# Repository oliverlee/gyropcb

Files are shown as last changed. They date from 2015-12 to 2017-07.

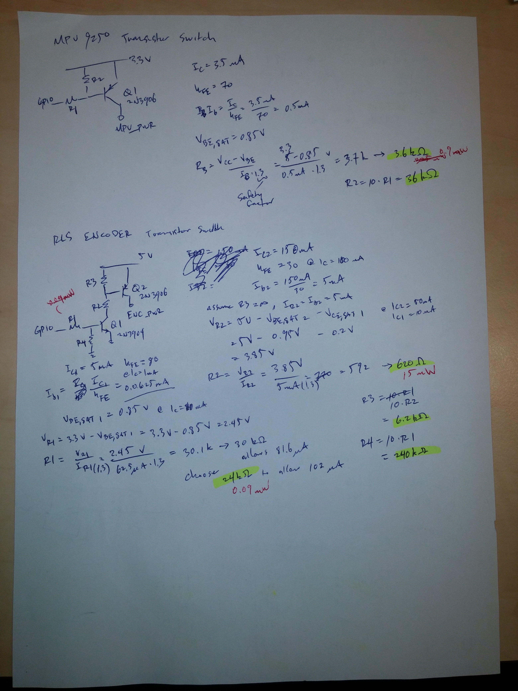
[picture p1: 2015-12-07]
design/IMG_20151120_180757.jpg

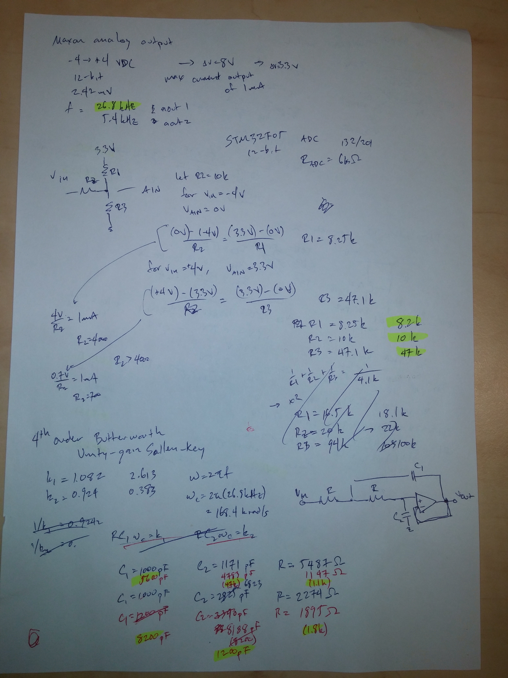
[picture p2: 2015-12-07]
design/IMG_20151120_180812.jpg

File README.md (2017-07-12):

This set of PCBs are designed to use with various projects in the
[phobos](https://github.com/oliverlee/phobos) repository. The PCBs are designed
to be used with the following items:
- [OLIMEX STM32-H405](https://www.olimex.com/Products/ARM/ST/STM32-H405/)
- [Maxon ESCON Module 50//5](http://www.maxonmotor.com/maxon/view/product/control/4-Q-Servokontroller/438725)

## Bill of Materials
The bill of materials is maintained [here](https://docs.google.com/spreadsheets/d/1CJe4dBAEXy64Y3e8YSP1X_Nll6x3aowWz7-QJbUk4VQ/edit?usp=sharing)

It may be out of date so take a look at it carefully.

## Notes
- In order to use the SDIO peripheral, R27 on the OLIMEX STM32-H405 must be
  disconnected from from the SDIO_CMD line (EXT1-11). This can be done by
  cutting the trace connecting EXT1-11 and R27.

## Errata
### v0.1
### mc pcb
- Description for solder jumper switch S3 on silkscreen layer is reversed.
- Description for solder jumper switch S4 on silkscreen layer is reversed.
- SDIO CMD line missing pullup resistor. A 33k resistor can be added at EXT1
  connecting pins 5 and 11. The leads must be kept as short as possible to
  minimize overshoot and ringing.

### power pcb
- +24V mount pad not connected to +24V rail.
- GND mount pad not connected to ground planes.
- The measure line of the Kistler torque sensor cannot be pulled to ground. A
  fix requires the removal of transistor Q2 and the measure line to be connected
  to the collector end of transistor Q1. This bypasses and disables switch S1.
- Description for solder jumper switch S2 on silkscreen layer is reversed.
- Silkscreen on J1, J3 incorrect: WIND1 and WIND2 reversed.
- Trace for HALL2_S2 between Ext3 and J3 is completely missing.
- J1, J3 molex pins can not withstand motor windings 1,2,3 current. Motor windings cable must be connected directly to motor dive. Check drawing for new molex types used to rearrange the new connection.
- J1, J2 male molex vertical headers must be changed with right hand angle headers to allow motor drive fit to Ext2 & Ext1. Check drawing file for new headers used to make the rearrangement.

For the steer by wire bicycle project the following changes were made:
### power pcb
18 Voltage regulator switched from LM2576S TO LM2576HV to withstand higher voltage since power supply voltage was switched from 24v to 36v.
### mc_pcb
Multiplexers 74AC157D were removed since Giel mentioned that there was an issue with the supply voltage. 
The inputs and outputs pins of the multiplexers were connected with cables. U4 now gives an output of ENC1_CHA+CHB and ENC2_CHA+CHB. 
Rear wheel encoder must be connected directly to microcontroller. U5 gives the output of PEDAL_ENC_A +ENC_B.

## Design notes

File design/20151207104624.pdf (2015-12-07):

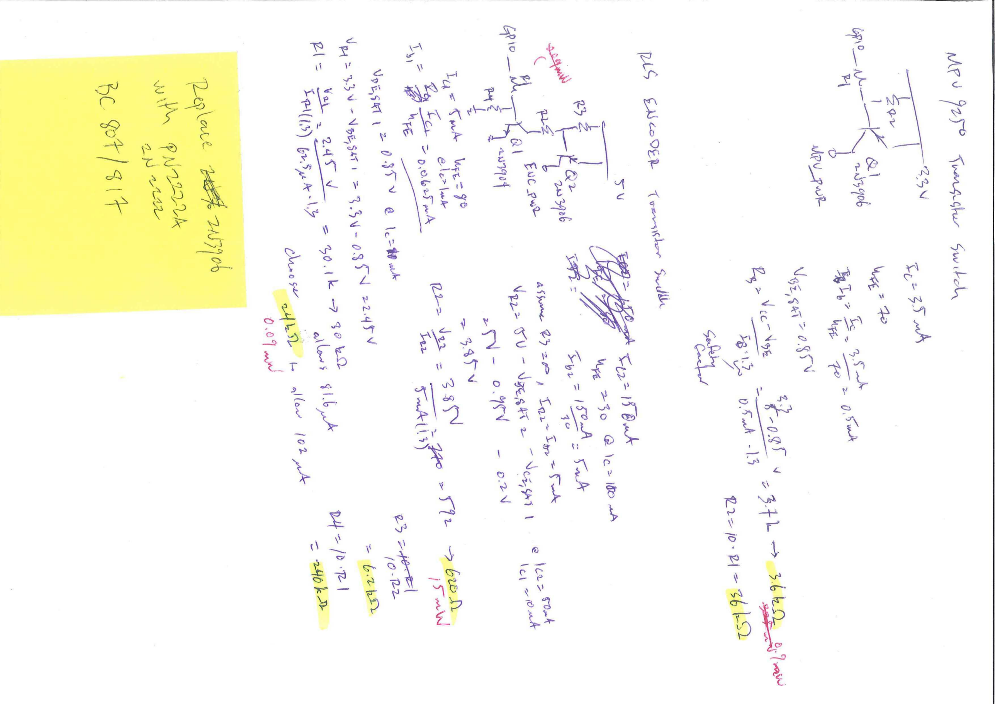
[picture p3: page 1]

- A

V
V

c

r
t

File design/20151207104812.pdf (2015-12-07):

5^

I

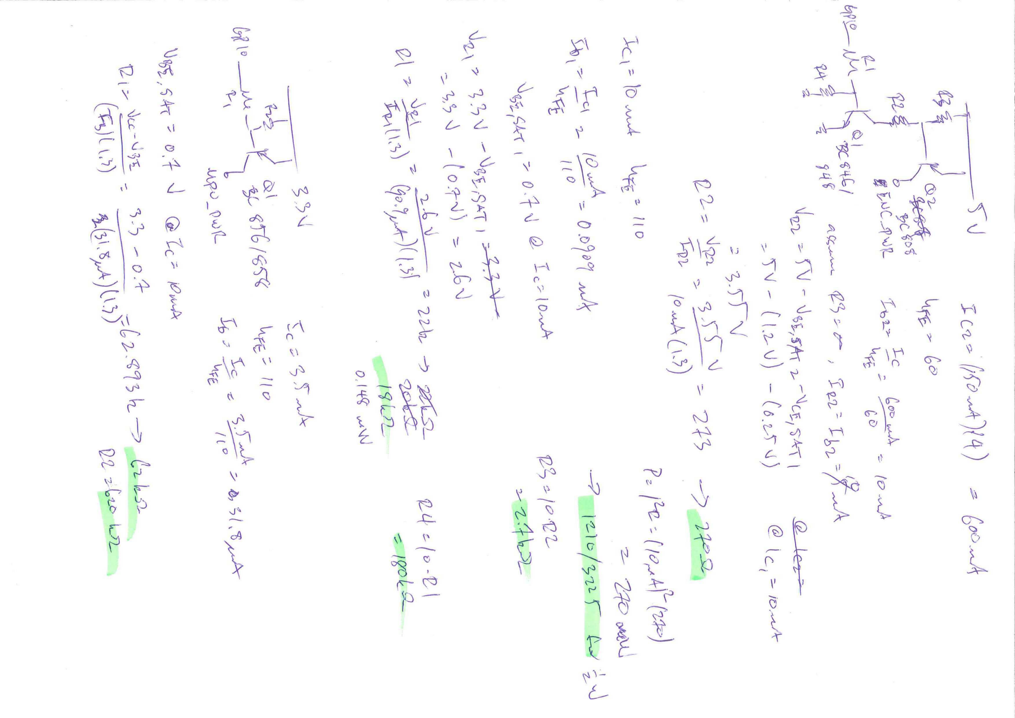
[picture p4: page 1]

I c -

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
0 | ^

4

'3
2

V
1 1 ^

1

&

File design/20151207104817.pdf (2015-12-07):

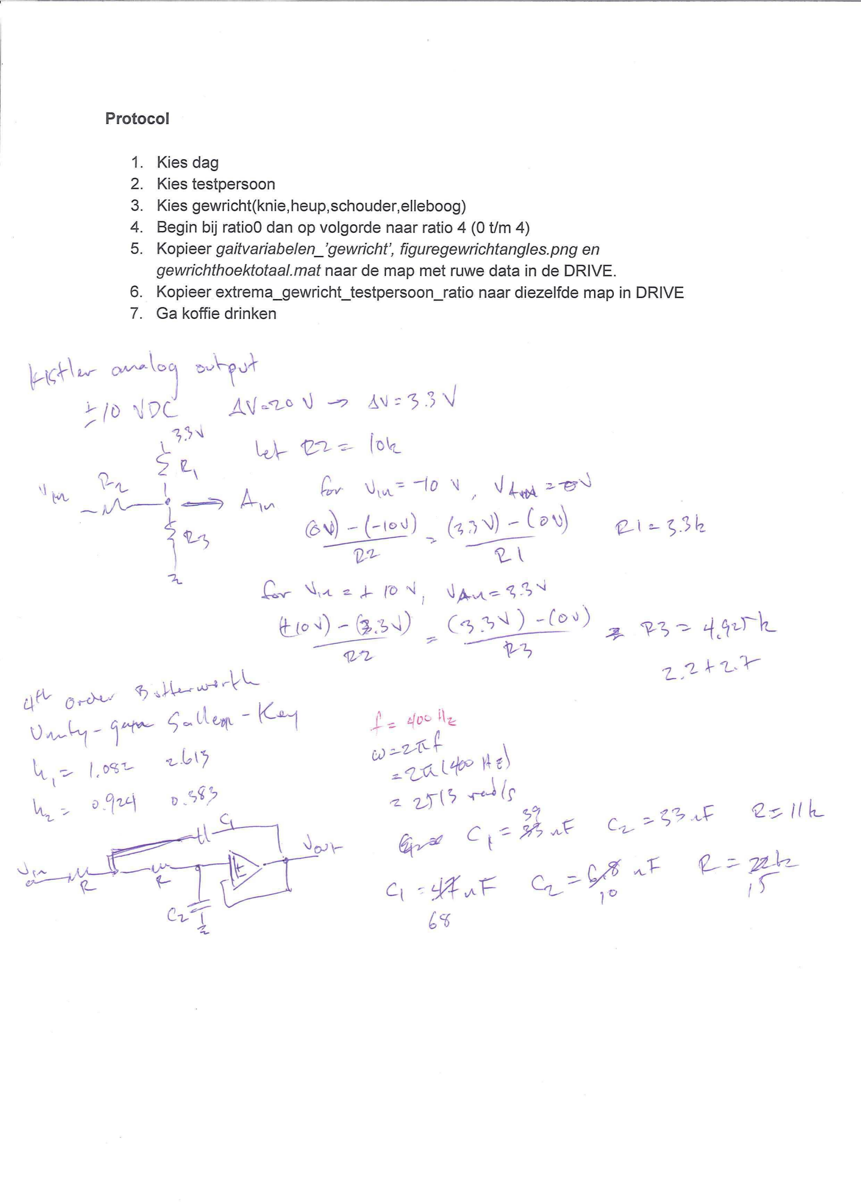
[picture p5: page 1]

Protocol

1. Kies dag
2. Kies testpersoon
3. Kies gewriclit(knie,heup,schouder,elleboog)
4. Begin bij ratioO dan op volgorde naar ratio 4 (O t/m 4)
5. Kopieer gaitvariabelen_'gewricht', | figuregewrichtangles.png | en
gewrichthoel<totaal.mat naar de map met ruwe data in de DRIVE.
6. Kopieer extrema_gewricht_testpersoon_ratio naar diezelfde map in DRIVE
7. Ga koffie drinken

O

### Cv- "O

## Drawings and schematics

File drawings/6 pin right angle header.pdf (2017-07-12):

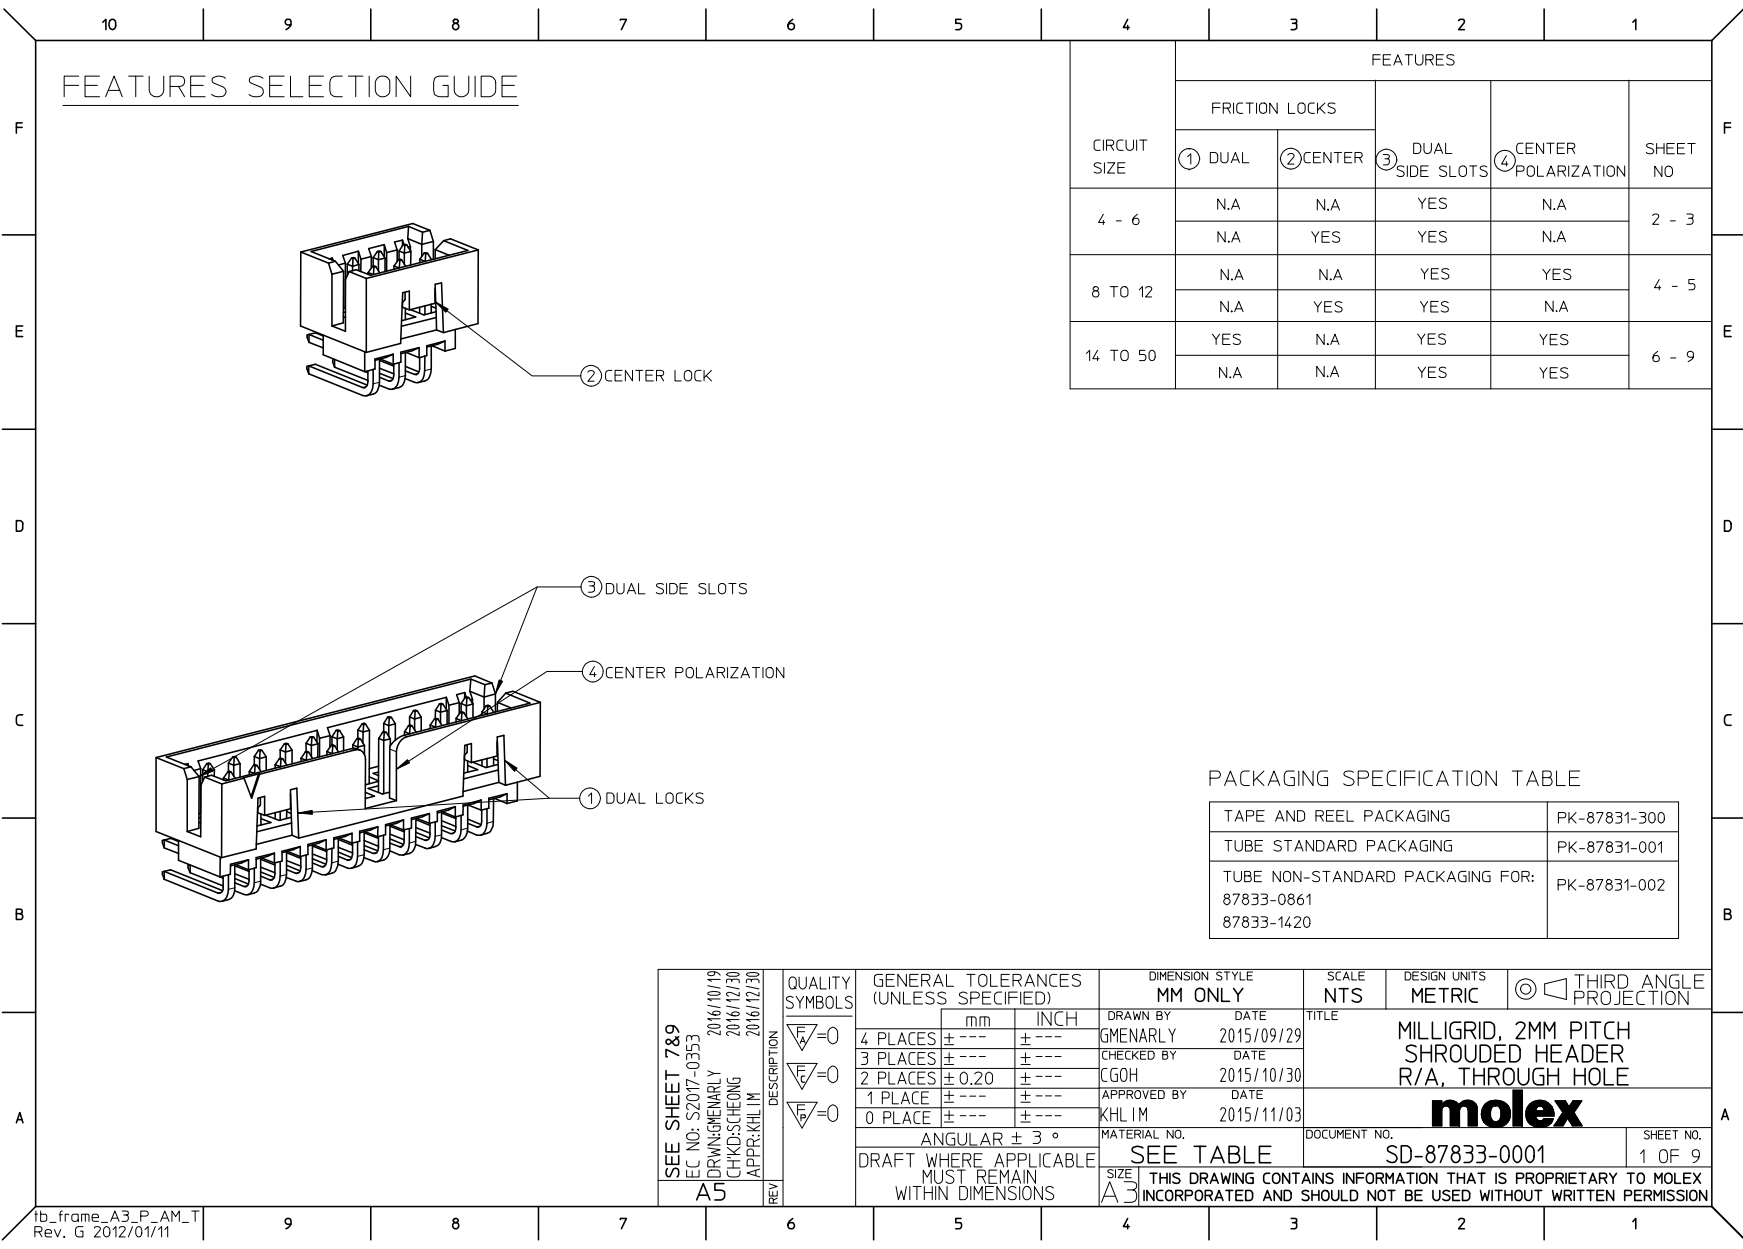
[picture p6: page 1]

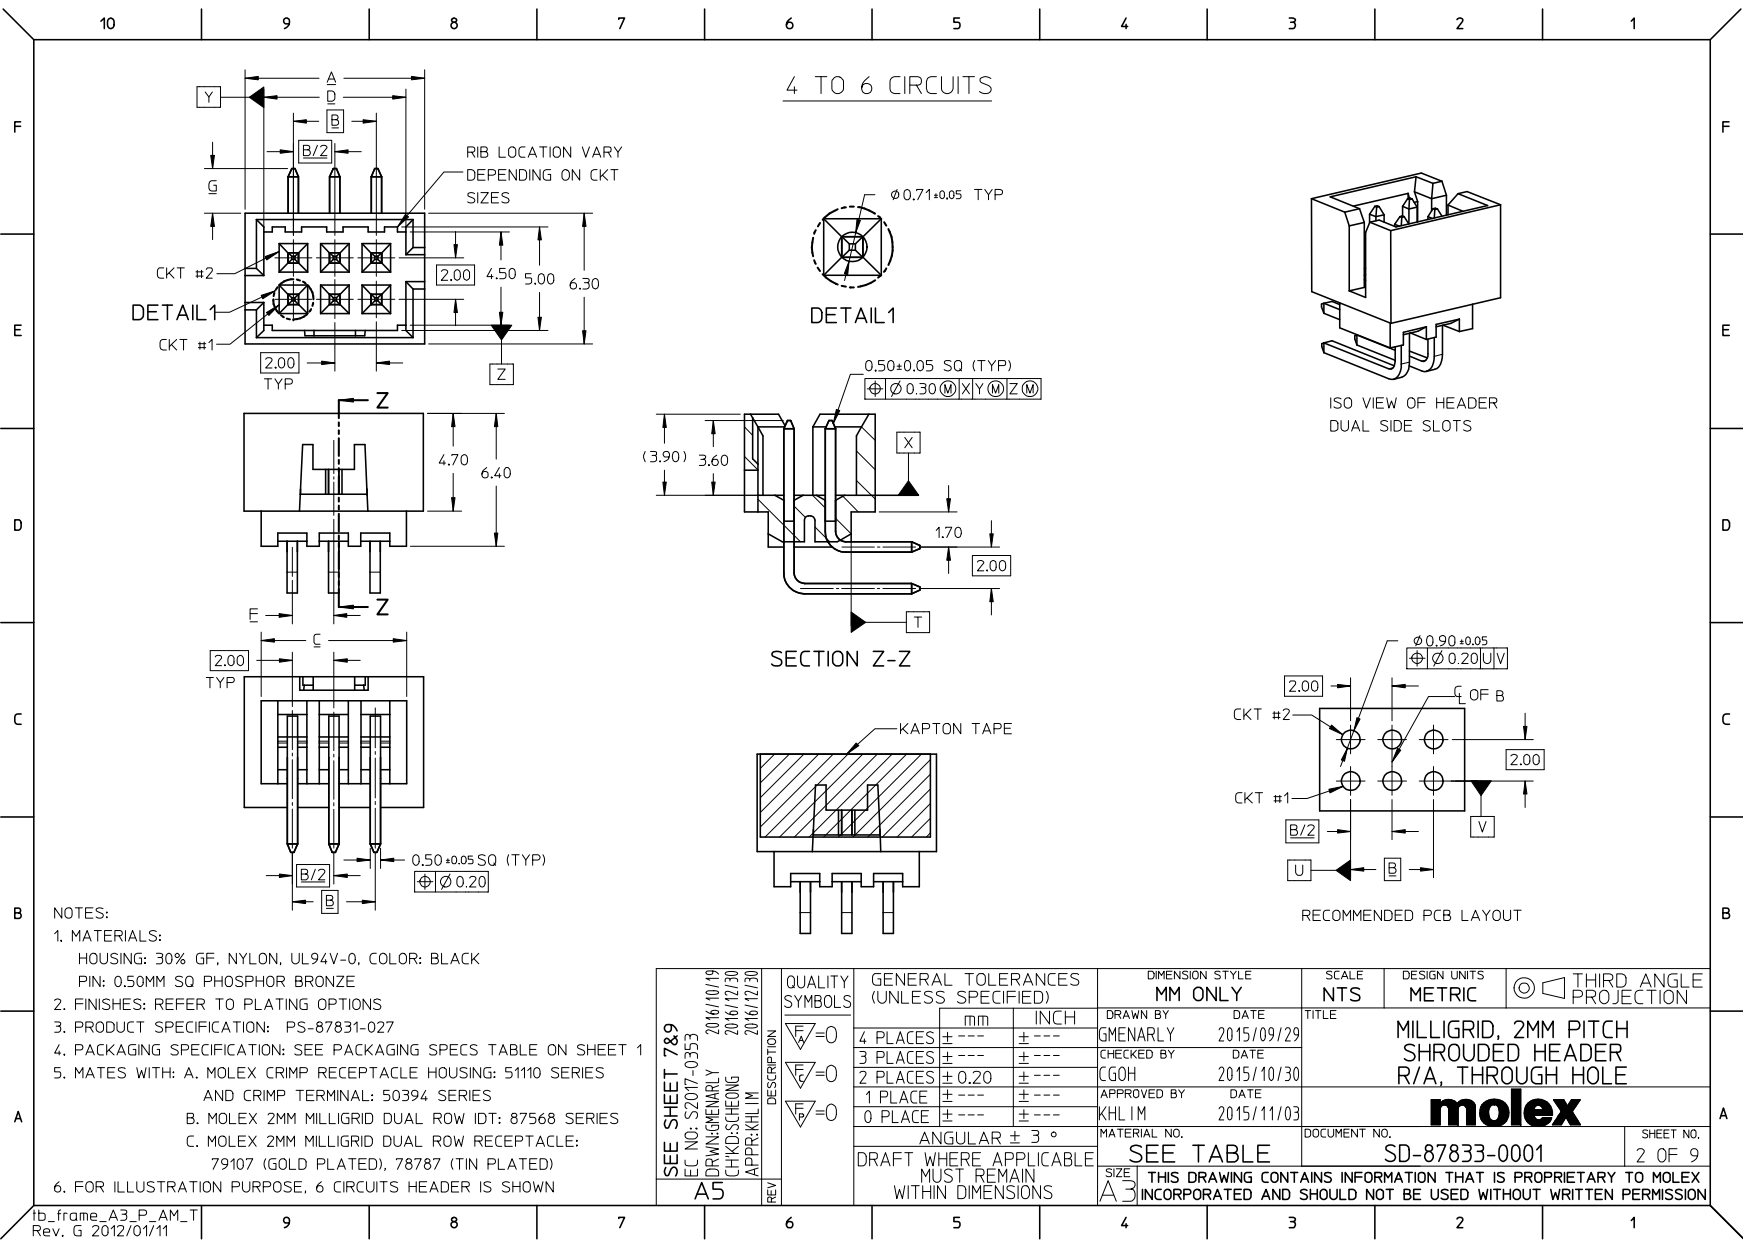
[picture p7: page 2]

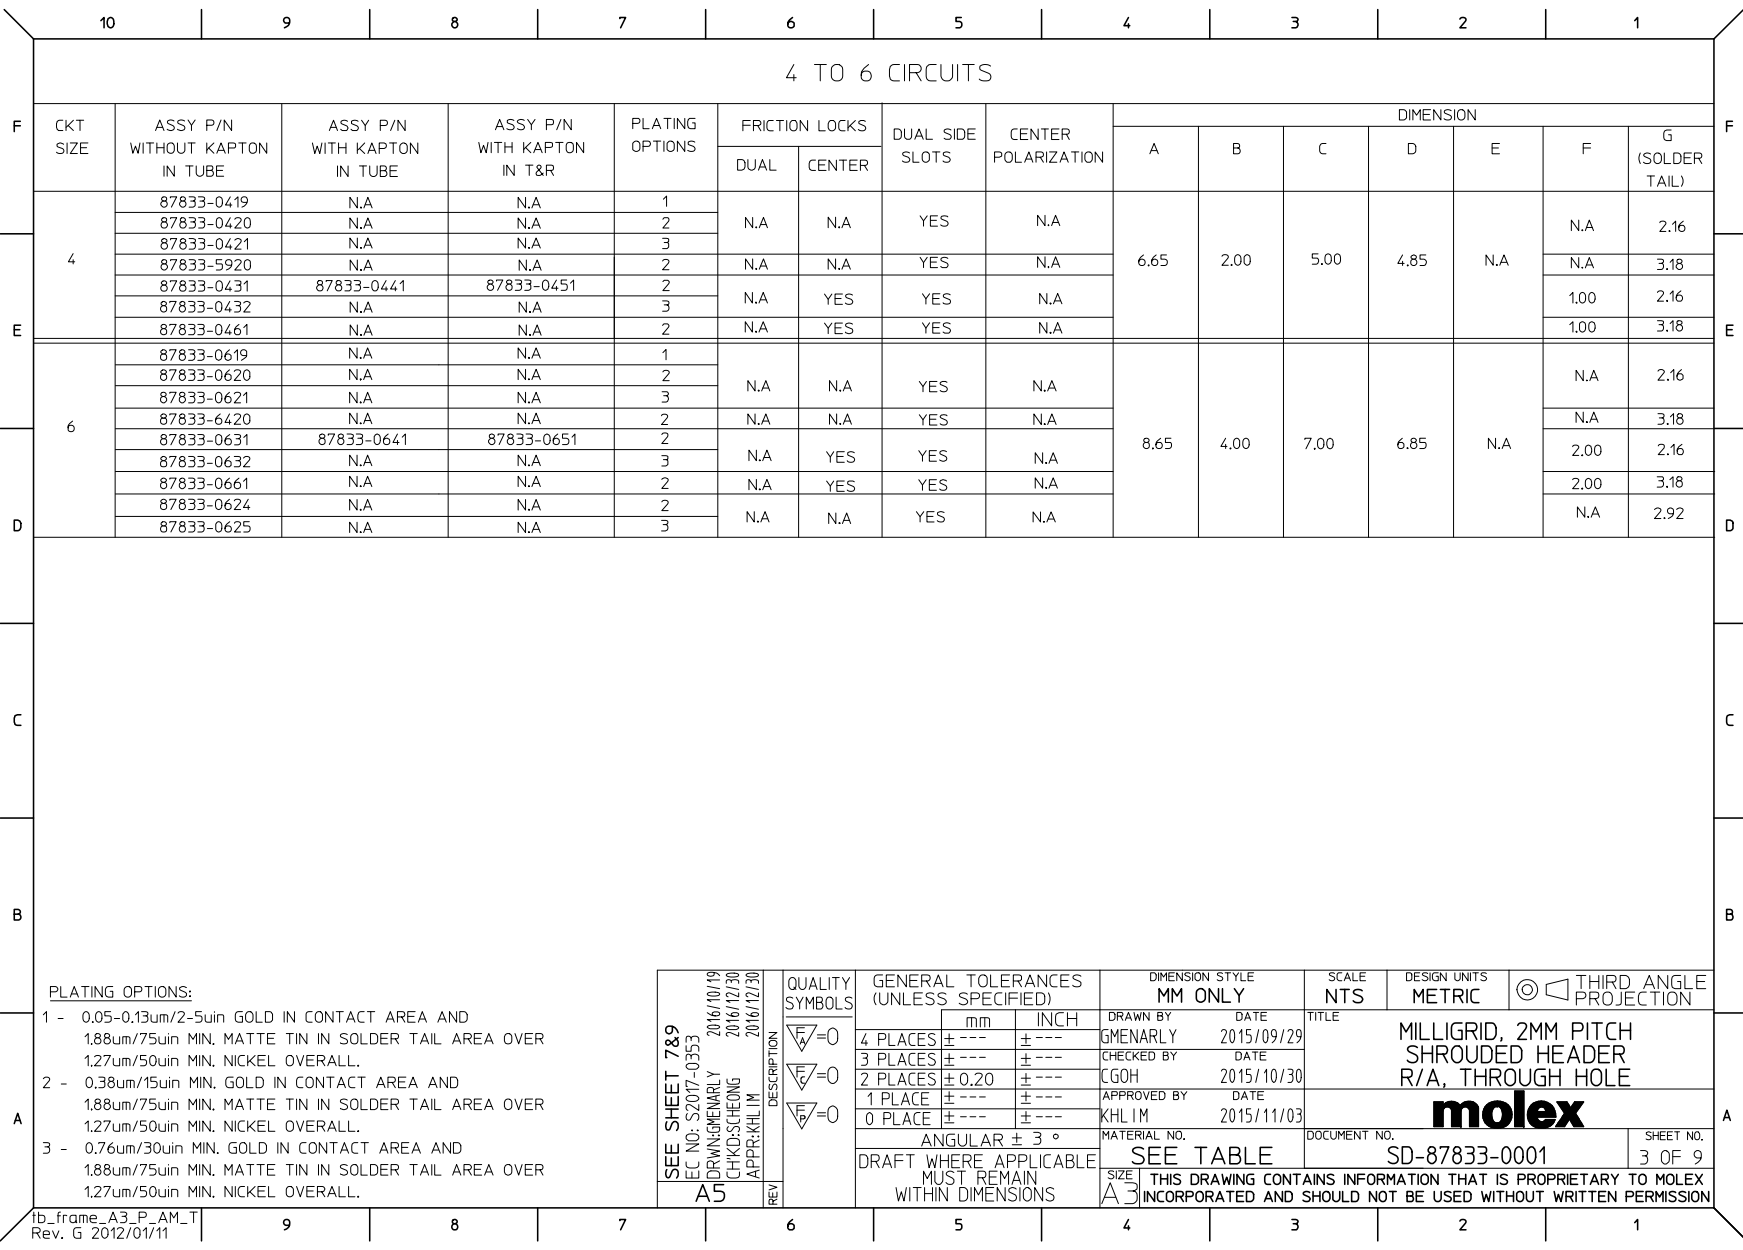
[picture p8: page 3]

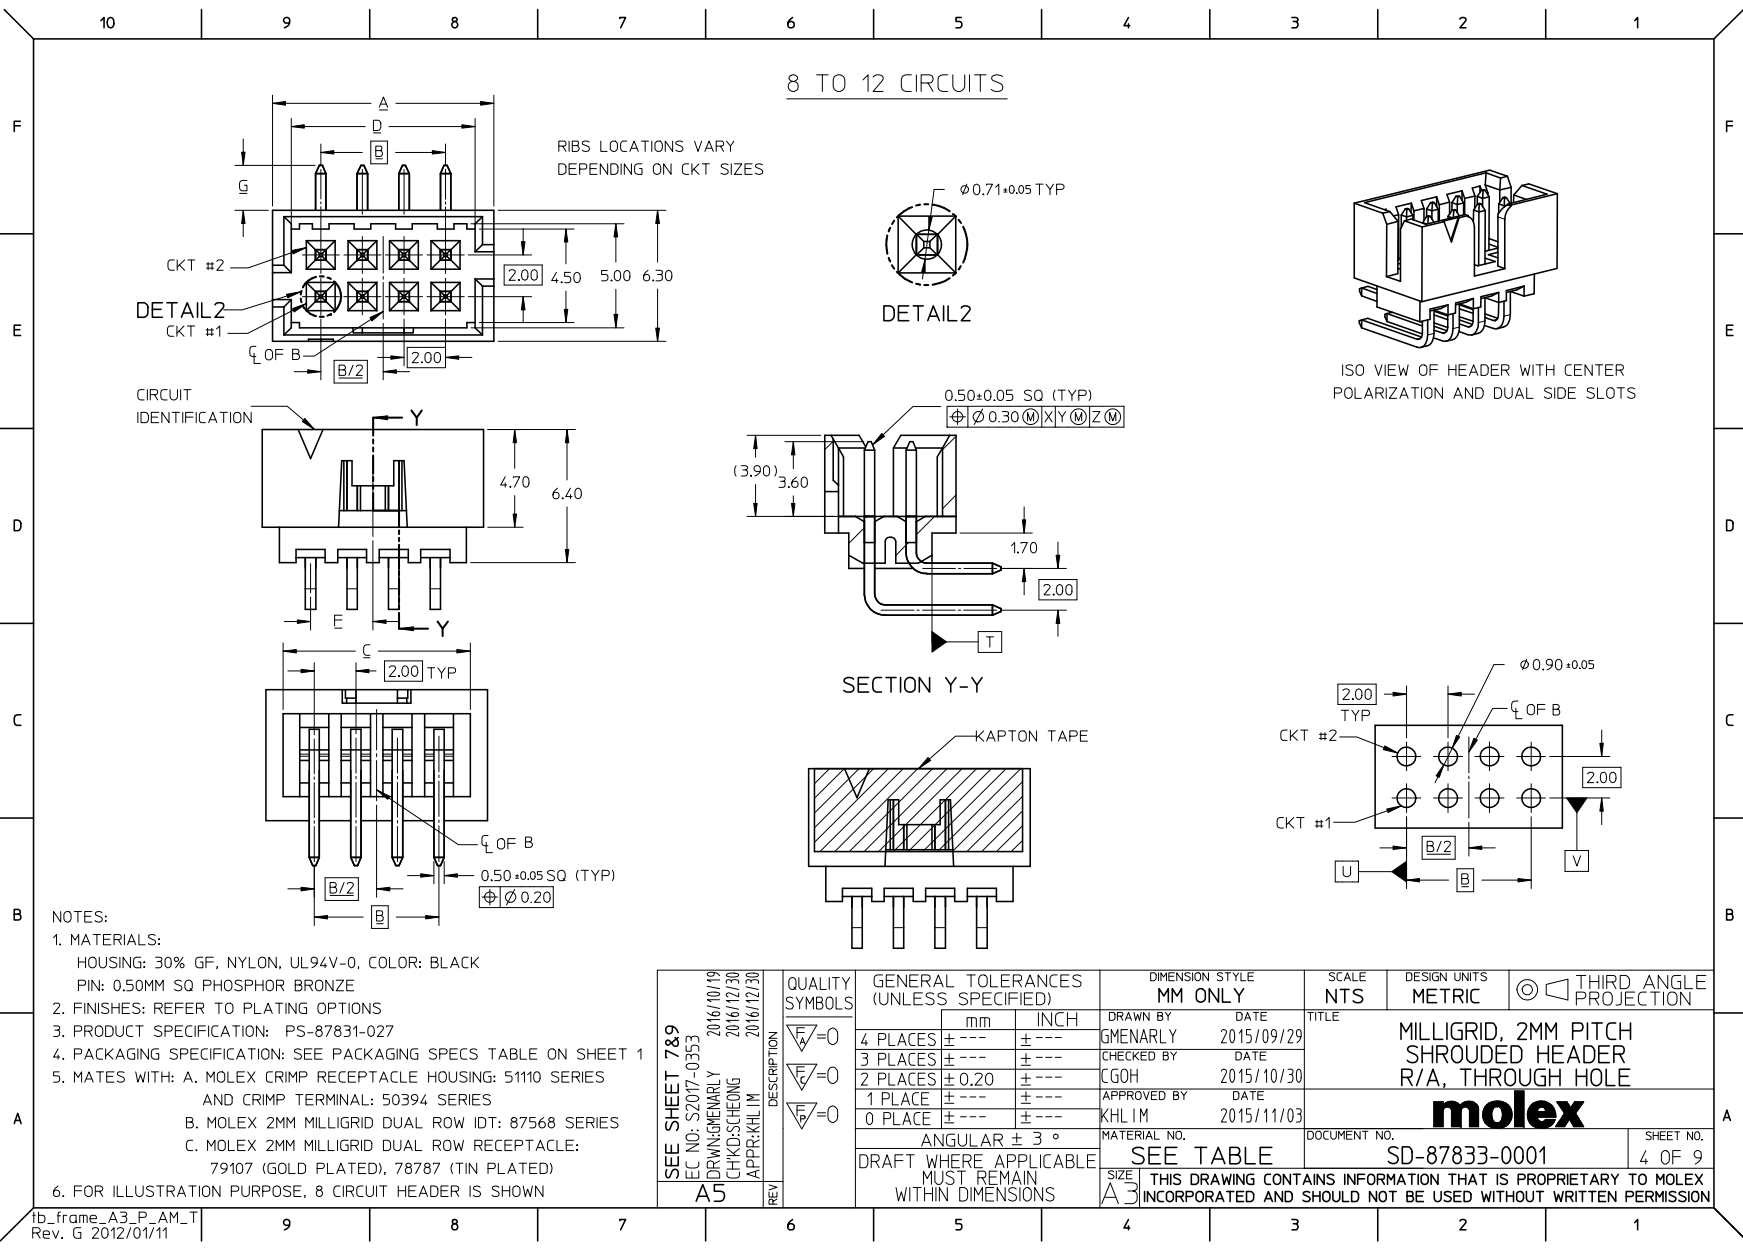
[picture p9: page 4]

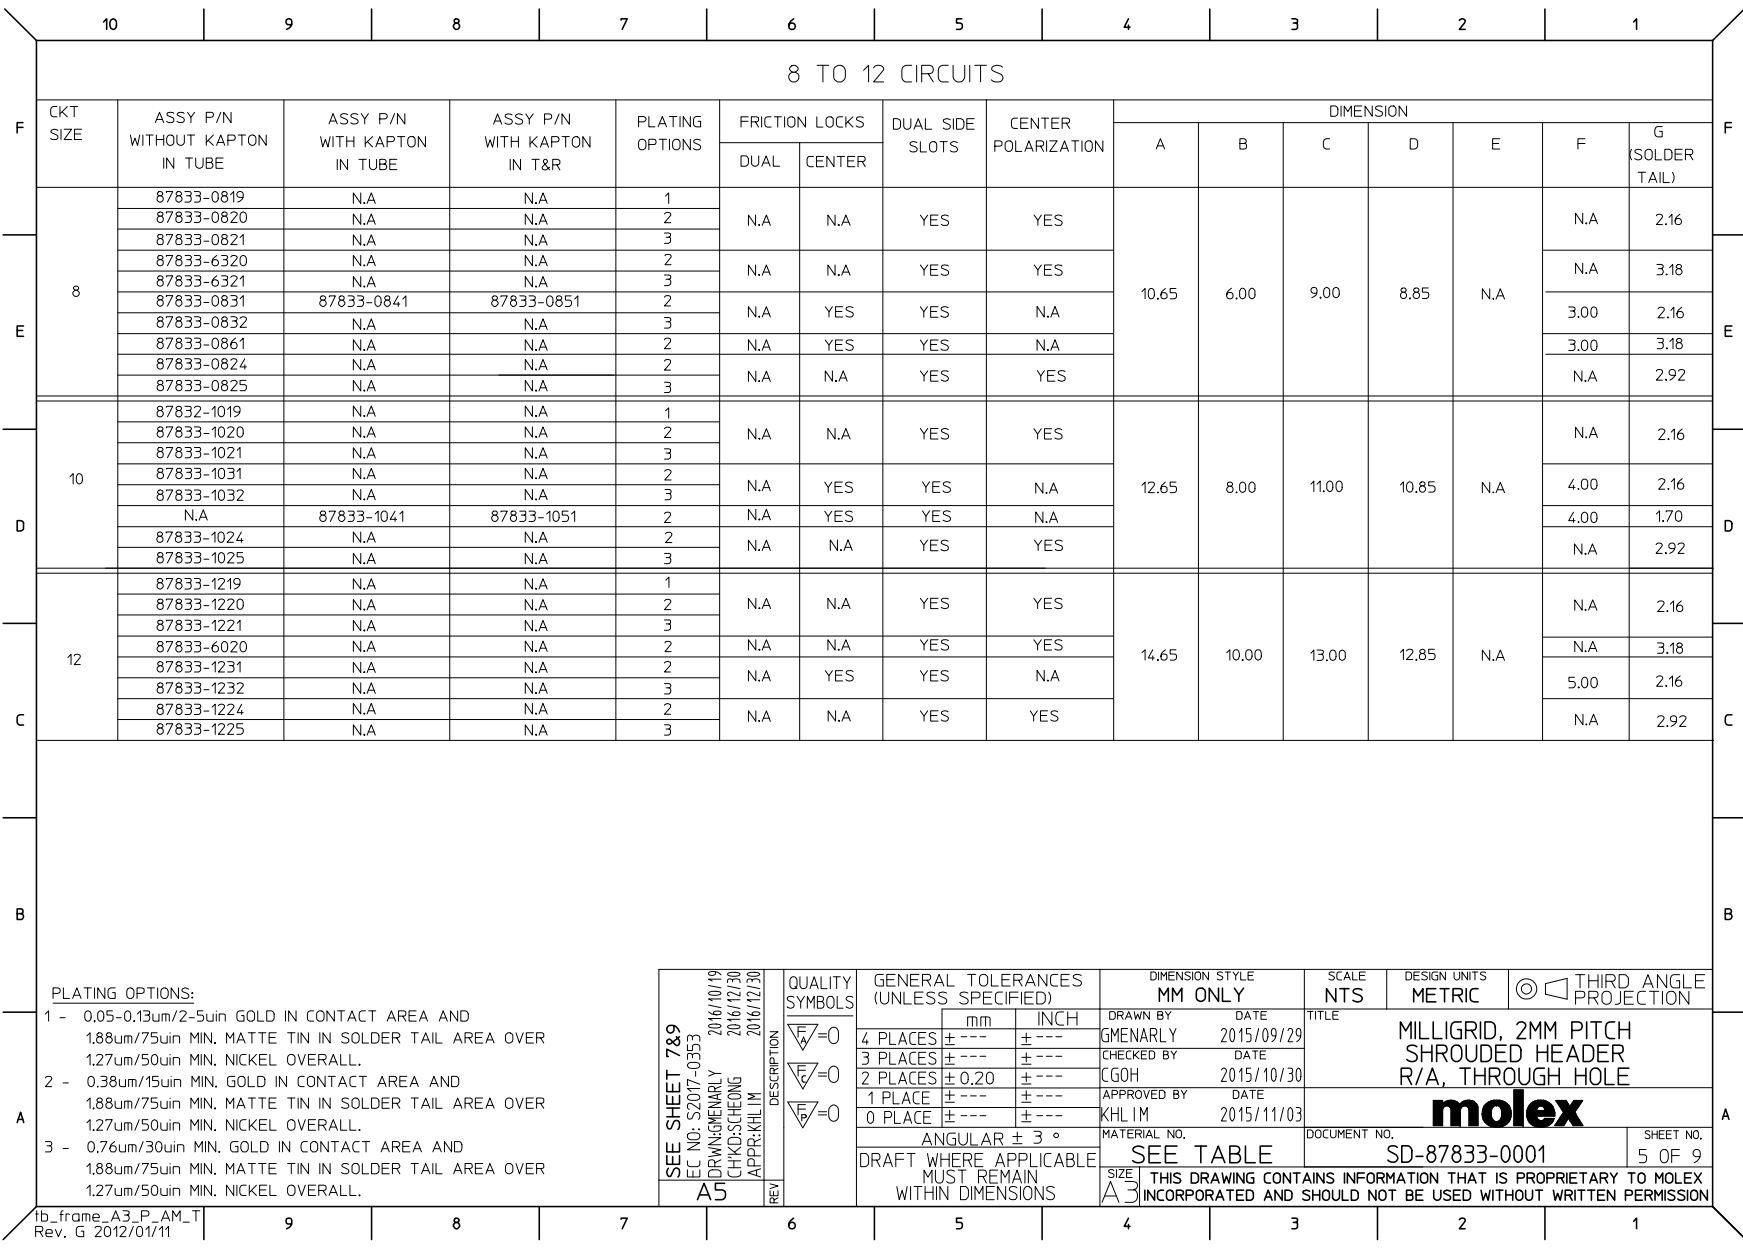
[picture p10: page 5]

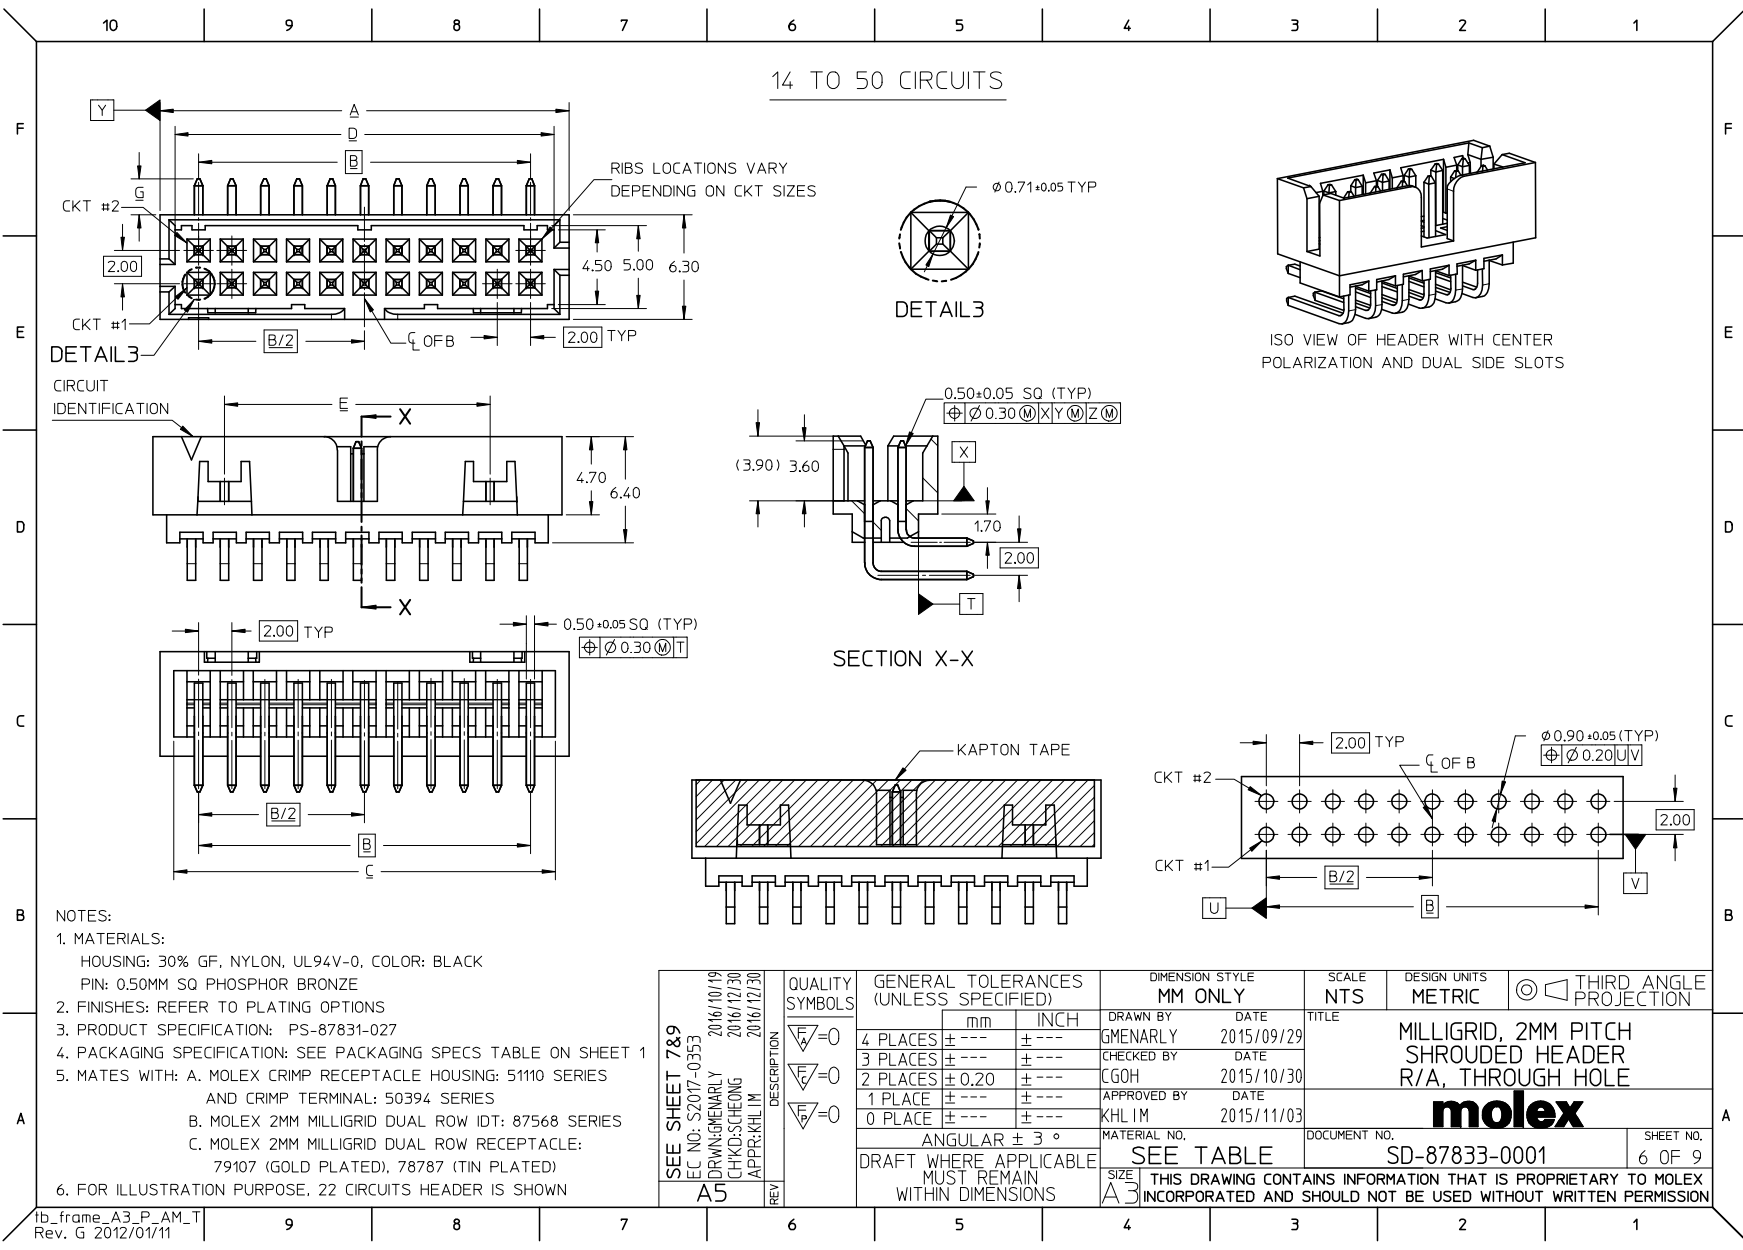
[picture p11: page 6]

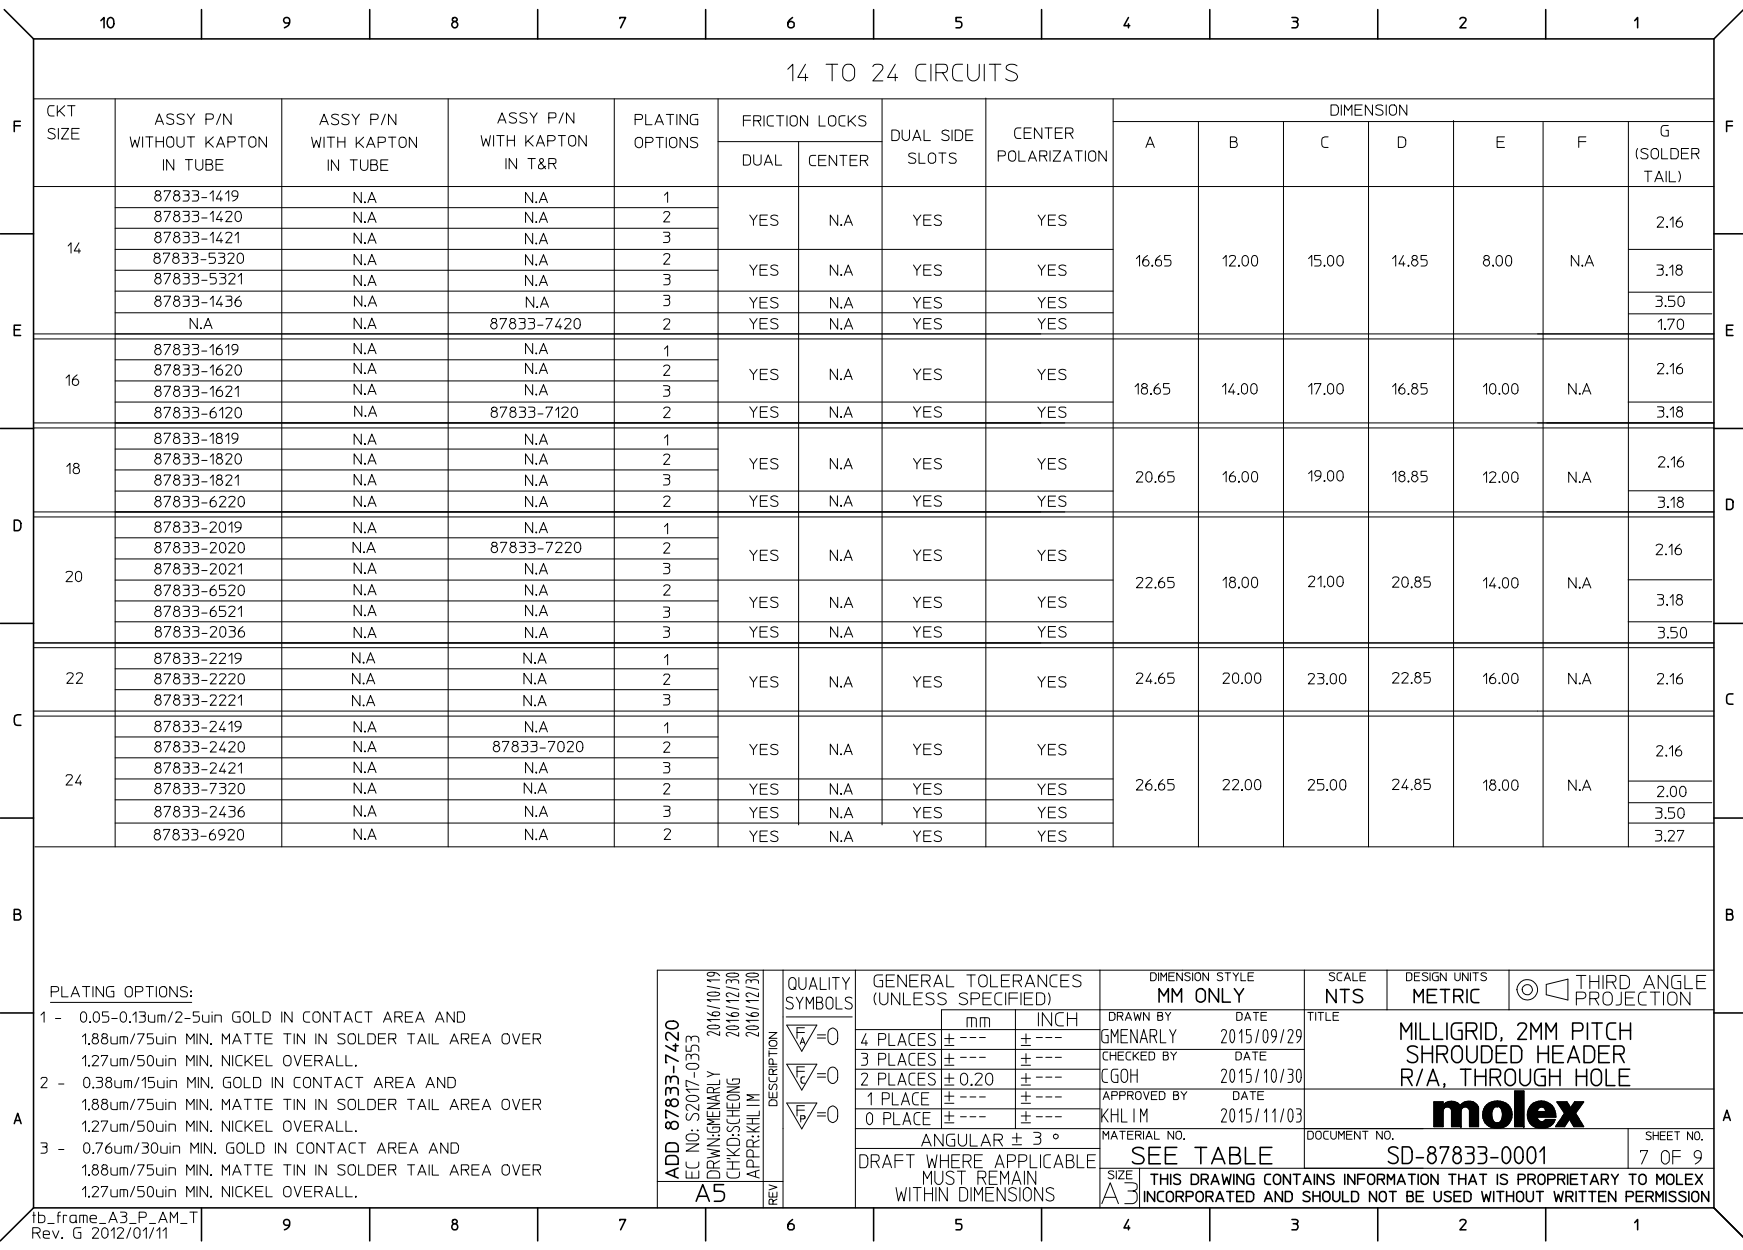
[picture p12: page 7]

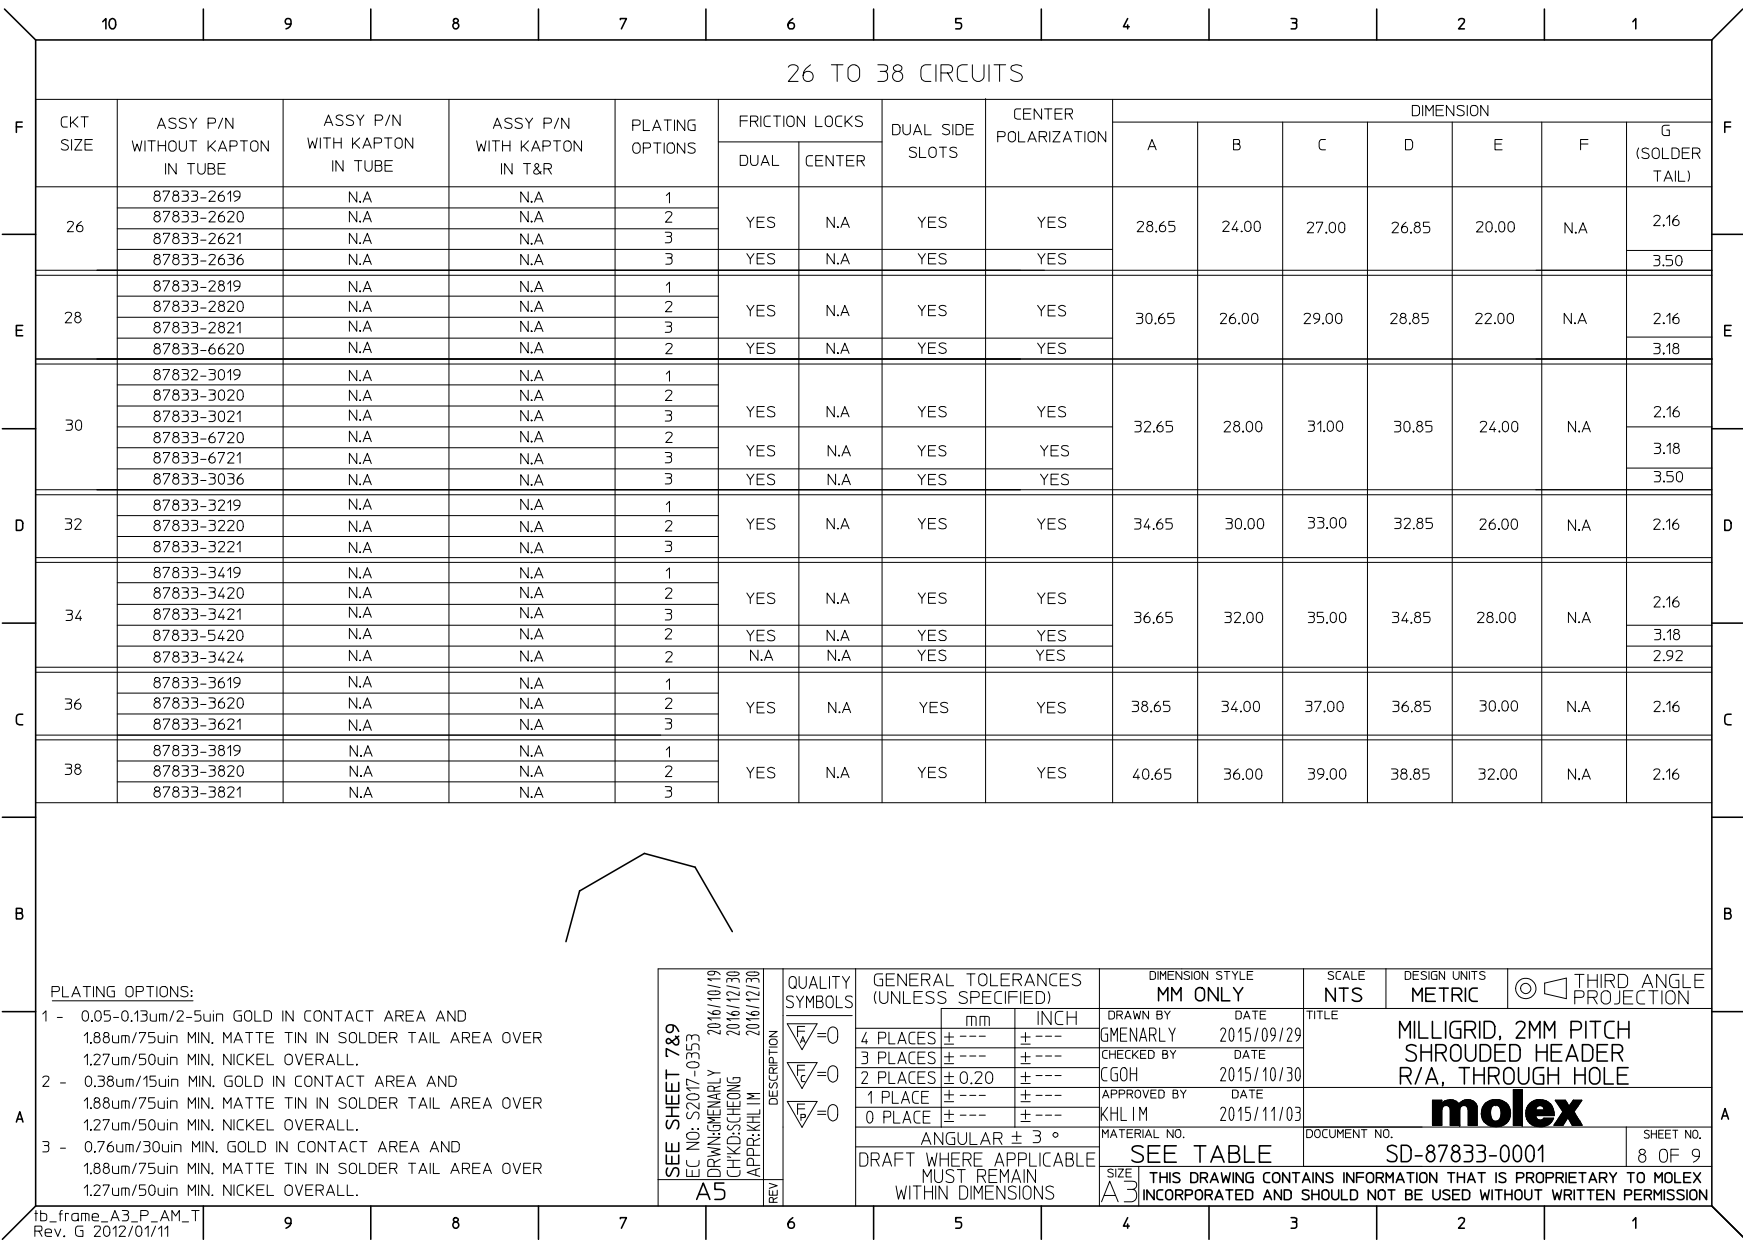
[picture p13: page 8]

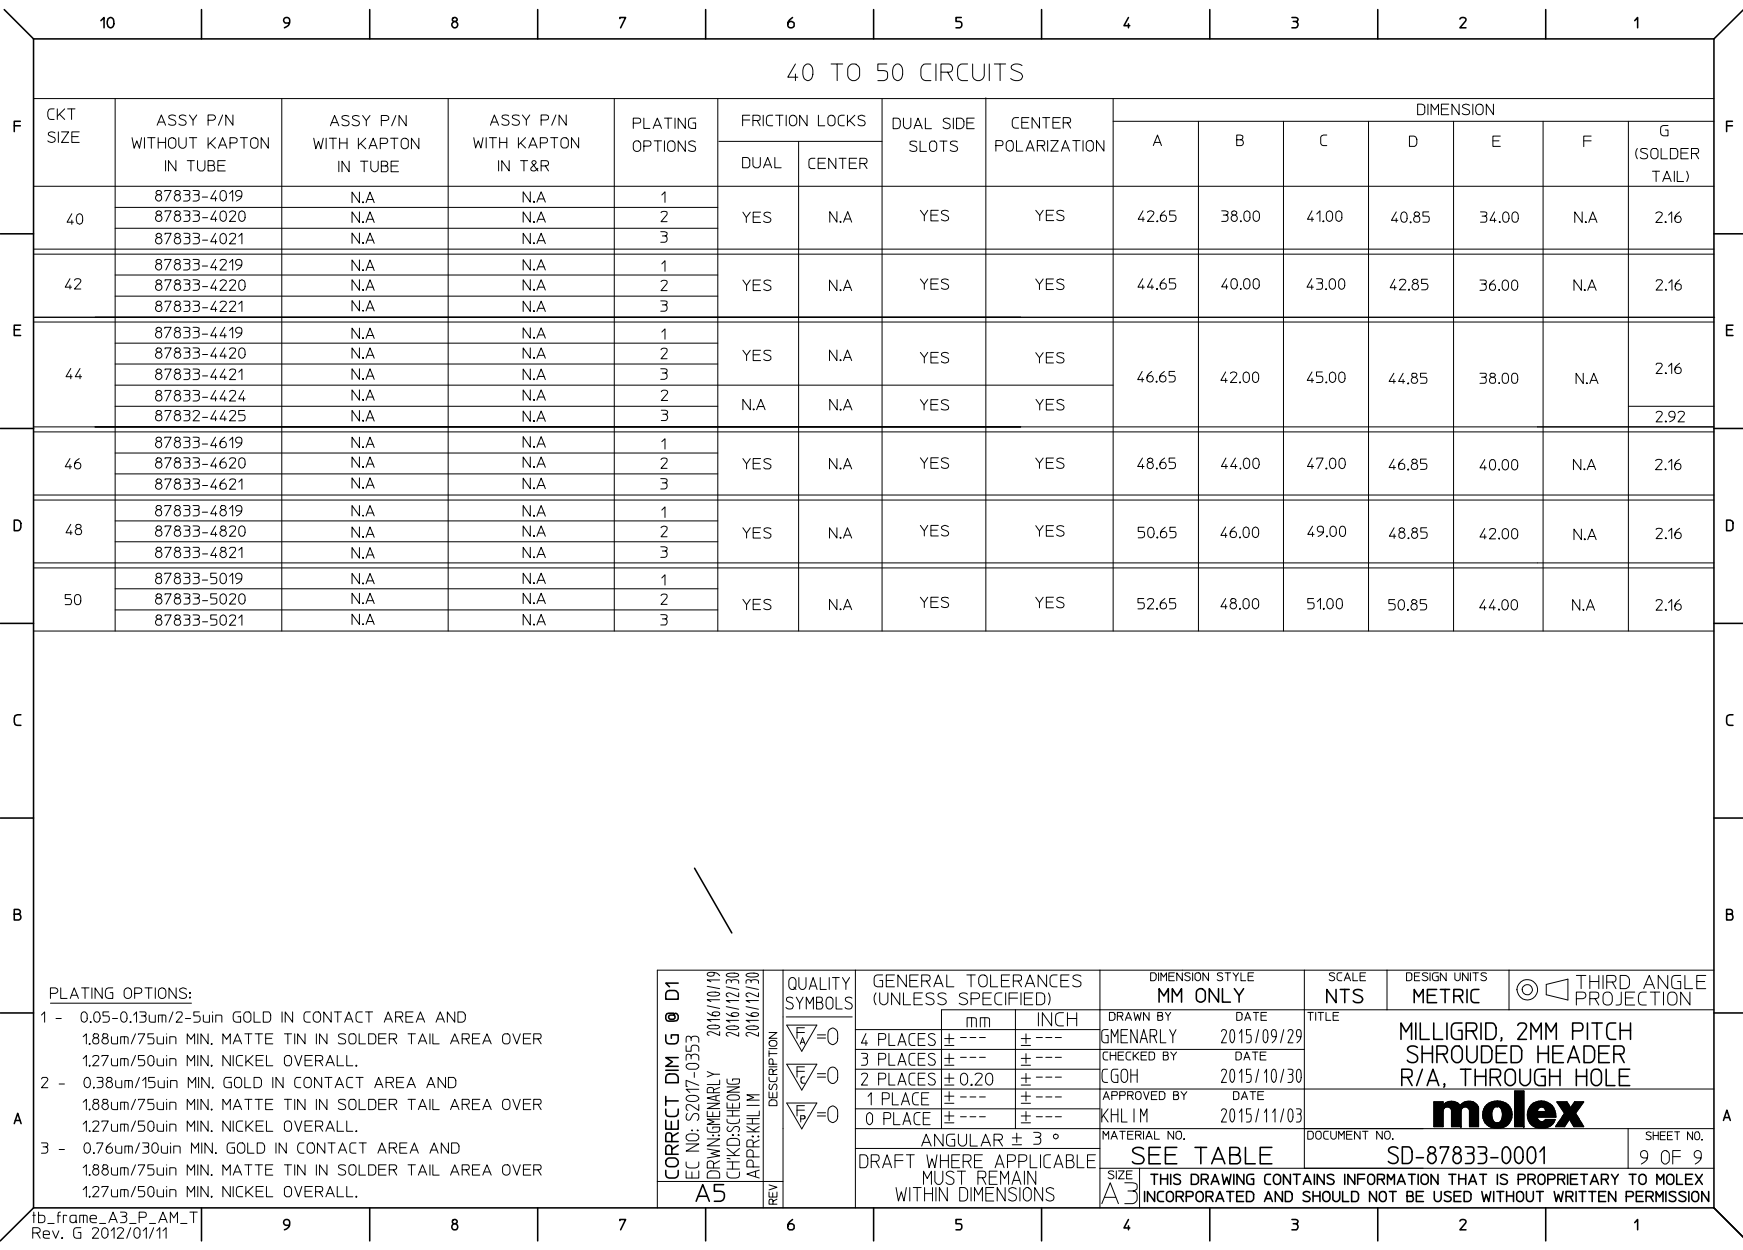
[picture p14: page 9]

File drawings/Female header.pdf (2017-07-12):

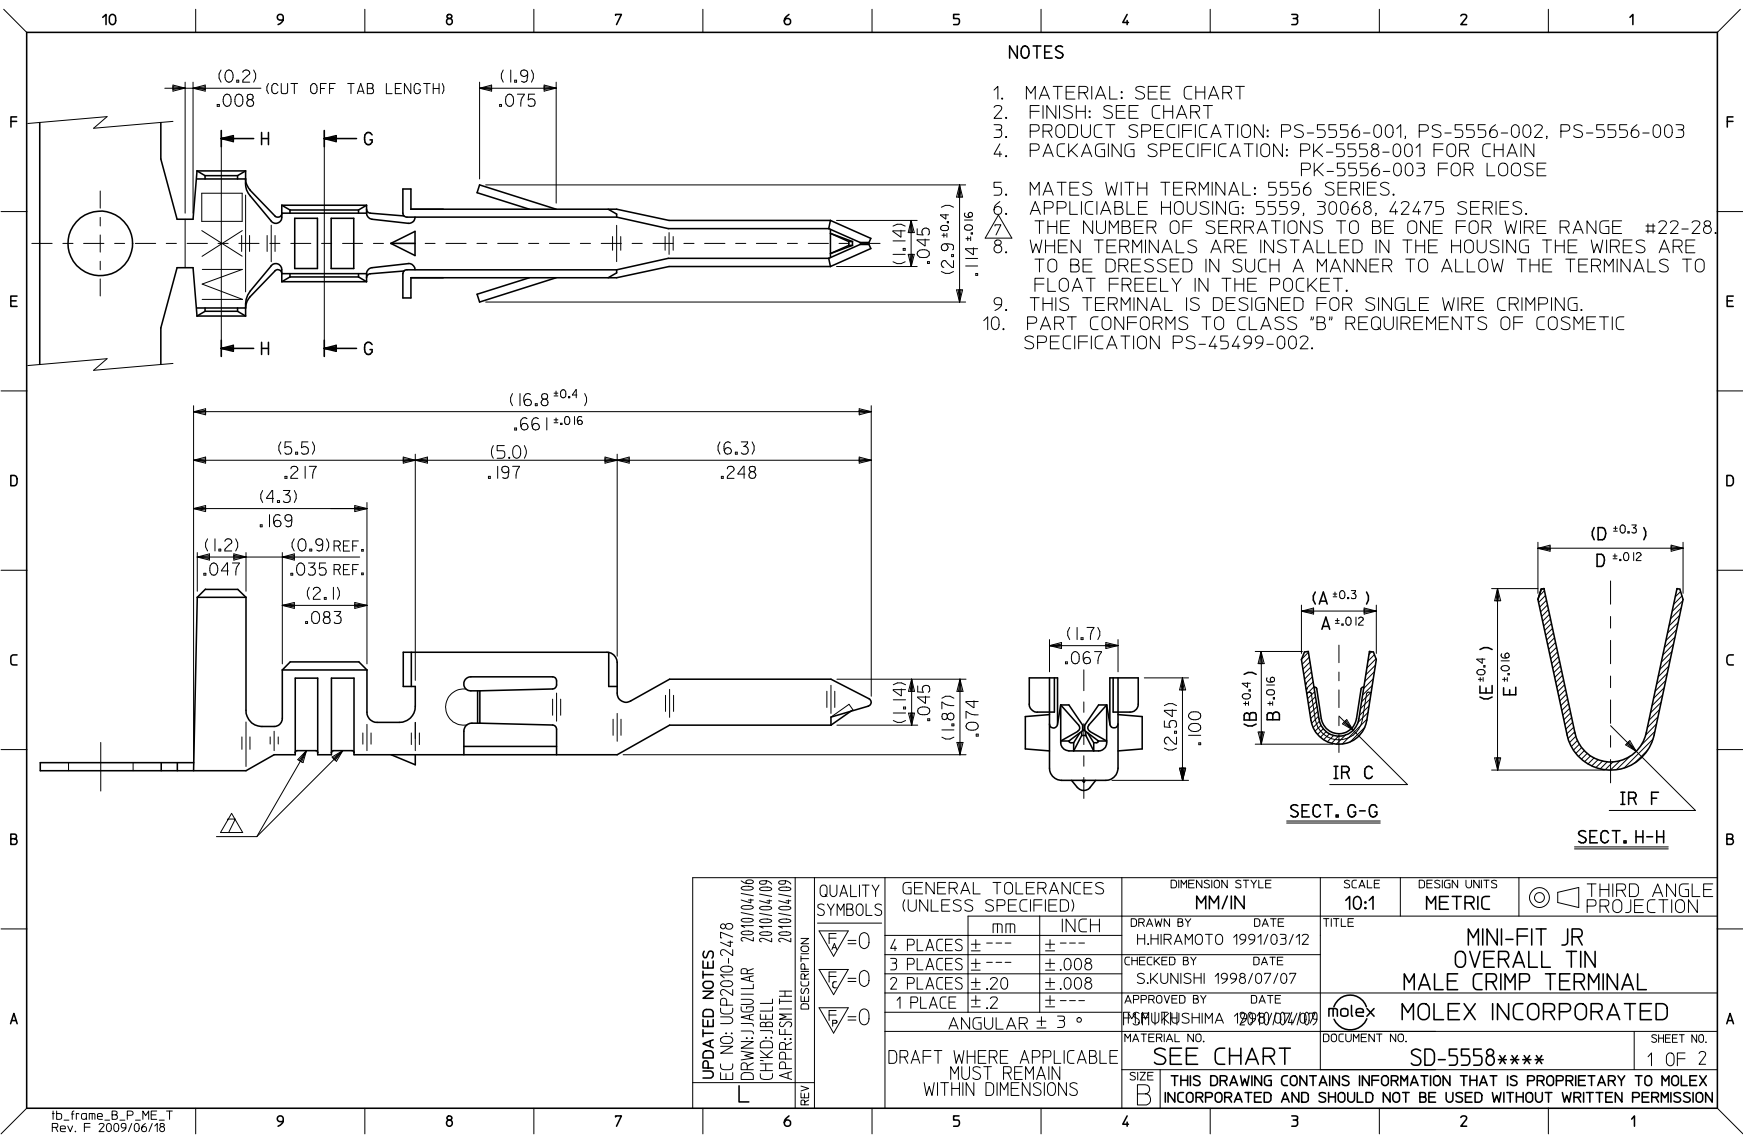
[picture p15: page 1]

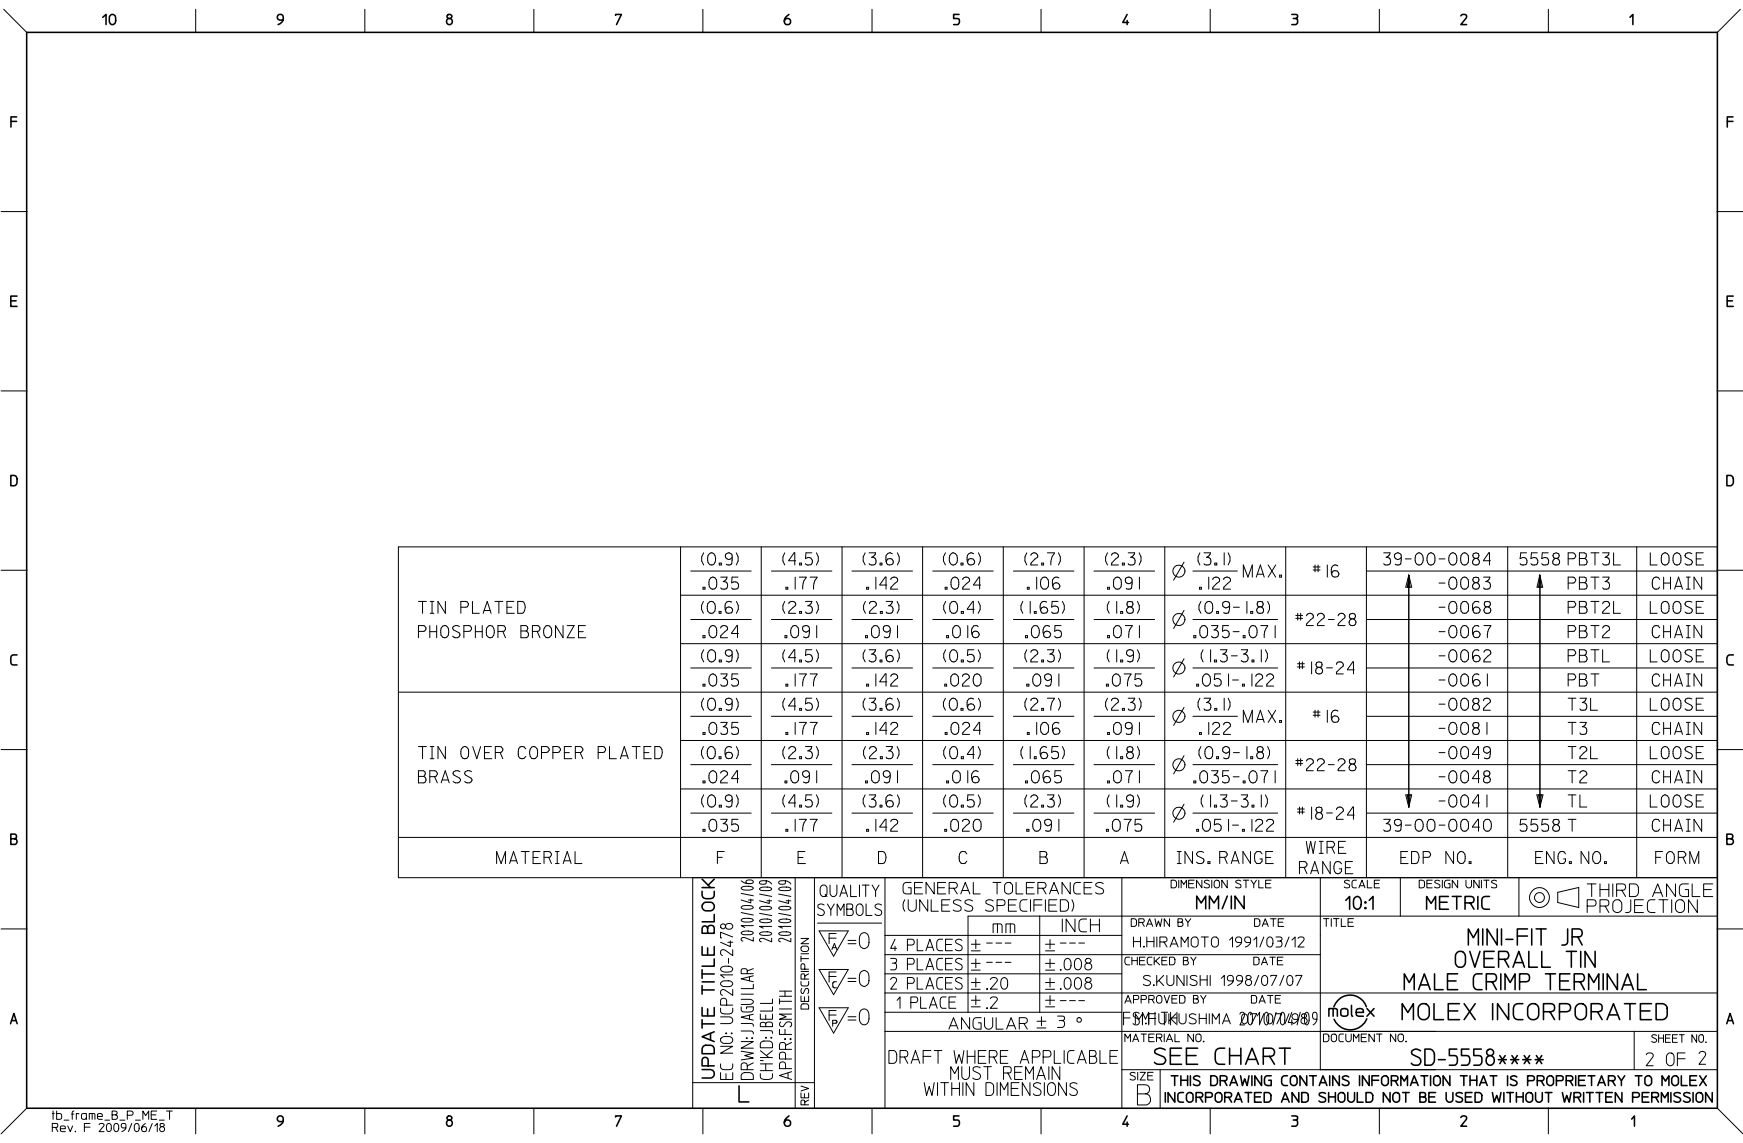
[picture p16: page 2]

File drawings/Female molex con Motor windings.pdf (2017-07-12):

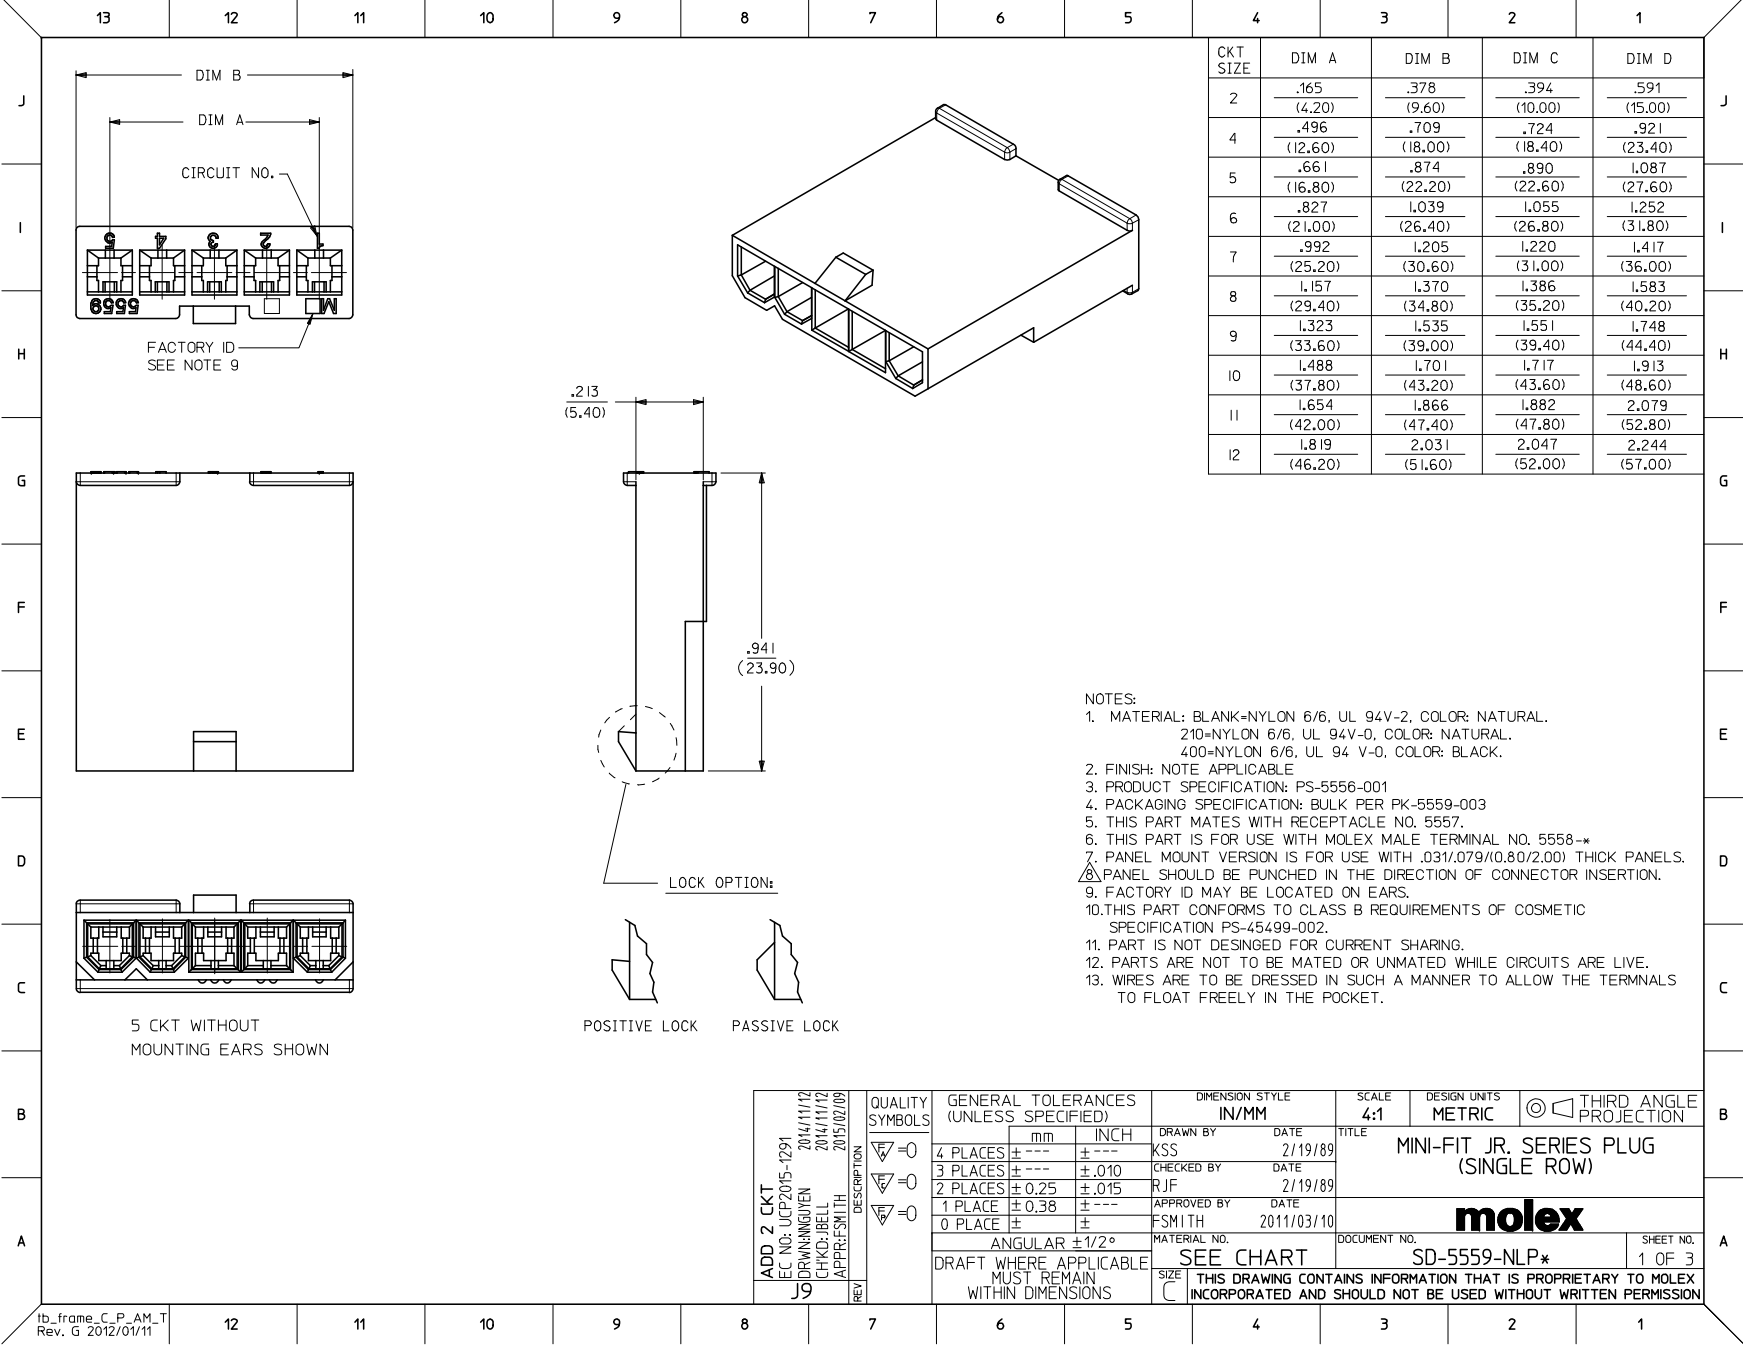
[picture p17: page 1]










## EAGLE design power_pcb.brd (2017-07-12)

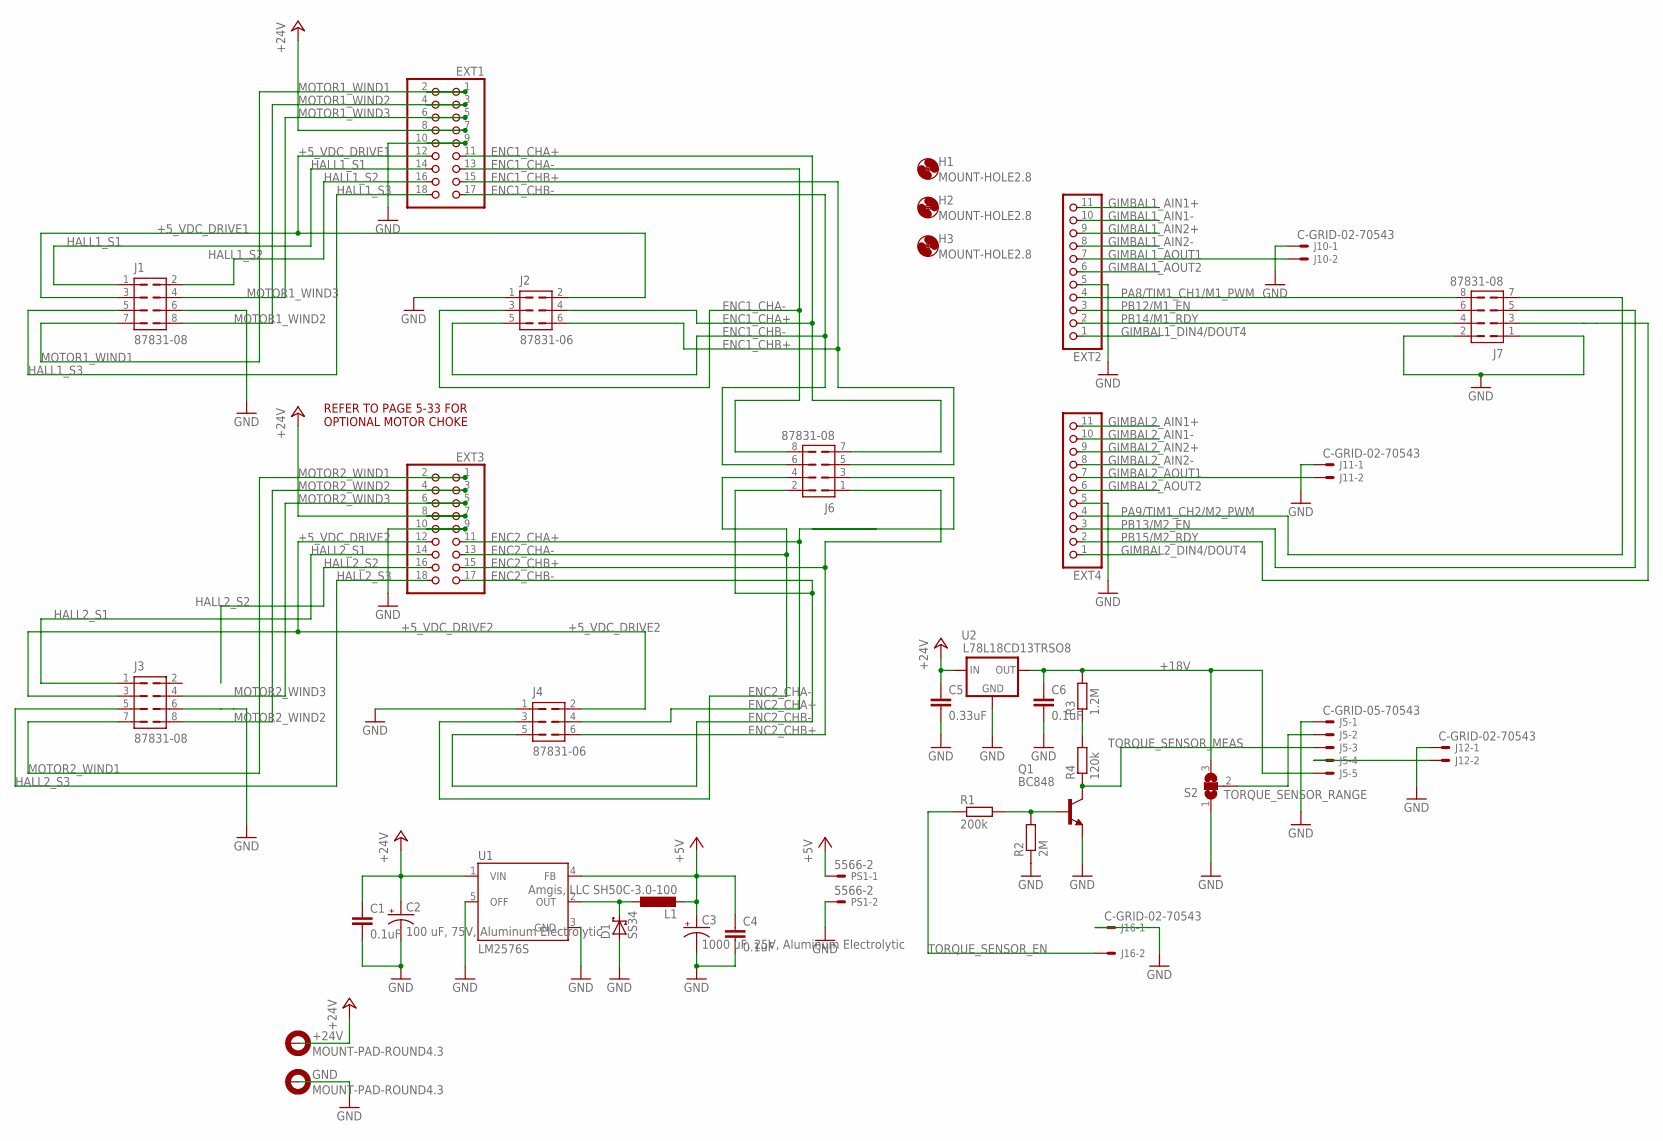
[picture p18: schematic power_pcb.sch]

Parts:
+24V: MOUNT-PAD-ROUND4.3; 4,3-PAD
C1, C4, C6: 0.1uF; C0603
C2: 100 uF, 75V, Aluminum Electrolytic; PANASONIC_H13
C3: 1000 uF, 25V, Aluminum Electrolytic; PANASONIC_H13
C5: 0.33uF; C0603
D1: SS34; SMC
EXT1, EXT3: PINHD-2X9; 2X09
EXT2, EXT4: PINHD-1X11; 1X11
GND: MOUNT-PAD-ROUND4.3; 4,3-PAD
H1, H2, H3: MOUNT-HOLE2.8; 2,8
J1, J3, J6, J7: 87831-08
J2, J4: 87831-06
J5: C-GRID-05-70543; 70543-05
J10, J11, J12, J16: C-GRID-02-70543; 70543-02
L1: Amgis, LLC SH50C-3.0-100; SH50C-C4
PS1: 5566-2
Q1: BC848; SOT23
R1: 200k; R0603
R2: 2M; R0603
R3: 1.2M; R1210
R4: 120k; R1210
S2: SJ2W; SJ_2
U1: LM2576S; TO263-5
U2: L78L18CD13TRSO8; SO8-VREG

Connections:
+5V: C3.+, C4.1, L1.P$2 (2), PS1.1, U1.4 (FB)
+5_VDC_DRIVE1: EXT1.12, J1.3, J2.2
+5_VDC_DRIVE2: EXT3.12, J3.3, J4.2
+18V: C6.1, J5.5, R3.2, S2.3, U2.1 (OUT)
+24V: C1.1, C2.+, C5.1, EXT1.7, EXT1.8, EXT3.7, EXT3.8, U1.1 (VIN), U2.8 (IN)
ENC1_CHA+: EXT1.11, J2.4, J6.7
ENC1_CHA-: EXT1.13, J2.3, J6.8
ENC1_CHB+: EXT1.15, J2.6, J6.5
ENC1_CHB-: EXT1.17, J2.5, J6.6
ENC2_CHA+: EXT3.11, J4.4, J6.3
ENC2_CHA-: EXT3.13, J4.3, J6.4
ENC2_CHB+: EXT3.15, J4.6, J6.1
ENC2_CHB-: EXT3.17, J4.5, J6.2
GIMBAL1_AIN1+: EXT2.11
GIMBAL1_AIN1-: EXT2.10
GIMBAL1_AIN2+: EXT2.9
GIMBAL1_AIN2-: EXT2.8
GIMBAL1_AOUT1: EXT2.7, J10.2
GIMBAL1_AOUT2: EXT2.6
GIMBAL1_DIN4/DOUT4: EXT2.1
GIMBAL2_AIN1+: EXT4.11
GIMBAL2_AIN1-: EXT4.10
GIMBAL2_AIN2+: EXT4.9
GIMBAL2_AIN2-: EXT4.8
GIMBAL2_AOUT1: EXT4.7, J11.2
GIMBAL2_AOUT2: EXT4.6
GIMBAL2_DIN4/DOUT4: EXT4.1
GND: C1.2, C2.-, C3.-, C4.2, C5.2, C6.2, D1.A, EXT1.9, EXT1.10, EXT2.5, EXT3.9, EXT3.10, EXT4.5, J1.6, J2.1, J3.6, J4.1, J5.1, J7.1, J7.2, J10.1, J11.1, J12.1, J16.1, PS1.2, Q1.2 (E), R2.1, S2.1, U1.3 (GND), U1.5 (OFF), U2.2 (GND), U2.3 (GND), U2.6 (GND), U2.7 (GND)
HALL1_S1: EXT1.14, J1.1
HALL1_S2: EXT1.16, J1.2
HALL1_S3: EXT1.18, J1.5
HALL2_S1: EXT3.14, J3.1
HALL2_S2: EXT3.16
HALL2_S3: EXT3.18, J3.5
MOTOR1_WIND1: EXT1.1, EXT1.2, J1.7
MOTOR1_WIND2: EXT1.3, EXT1.4, J1.8
MOTOR1_WIND3: EXT1.5, EXT1.6, J1.4
MOTOR2_WIND1: EXT3.1, EXT3.2, J3.7
MOTOR2_WIND2: EXT3.3, EXT3.4, J3.8
MOTOR2_WIND3: EXT3.5, EXT3.6, J3.4
unnamed: J5.4, J12.2
unnamed: D1.C, L1.P$1 (1), U1.2 (OUT)
unnamed: R3.1, R4.2
unnamed: Q1.1 (B), R1.2, R2.2
PA8/TIM1_CH1/M1_PWM: EXT2.4, J7.8
PA9/TIM1_CH2/M2_PWM: EXT4.4, J7.7
PB12/M1_EN: EXT2.3, J7.6
PB13/M2_EN: EXT4.3, J7.5
PB14/M1_RDY: EXT2.2, J7.4
PB15/M2_RDY: EXT4.2, J7.3
TORQUE_SENSOR_EN: J16.2, R1.1
TORQUE_SENSOR_MEAS: J5.3, Q1.3 (C), R4.1
TORQUE_SENSOR_RANGE: J5.2, S2.2

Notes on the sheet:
REFER TO PAGE 5-33 FOR OPTIONAL MOTOR CHOKE

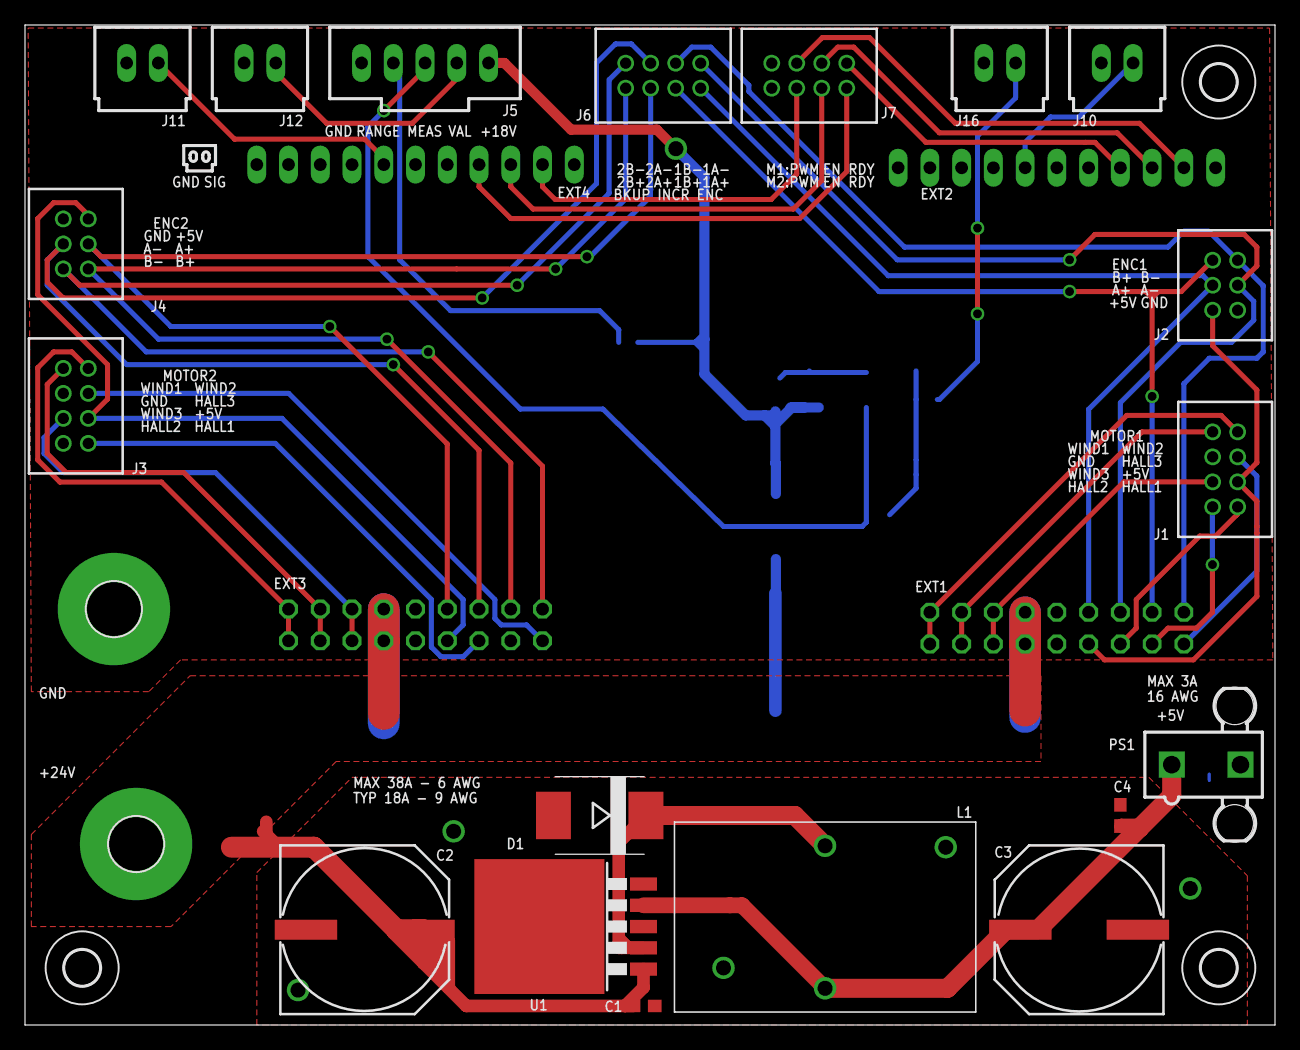
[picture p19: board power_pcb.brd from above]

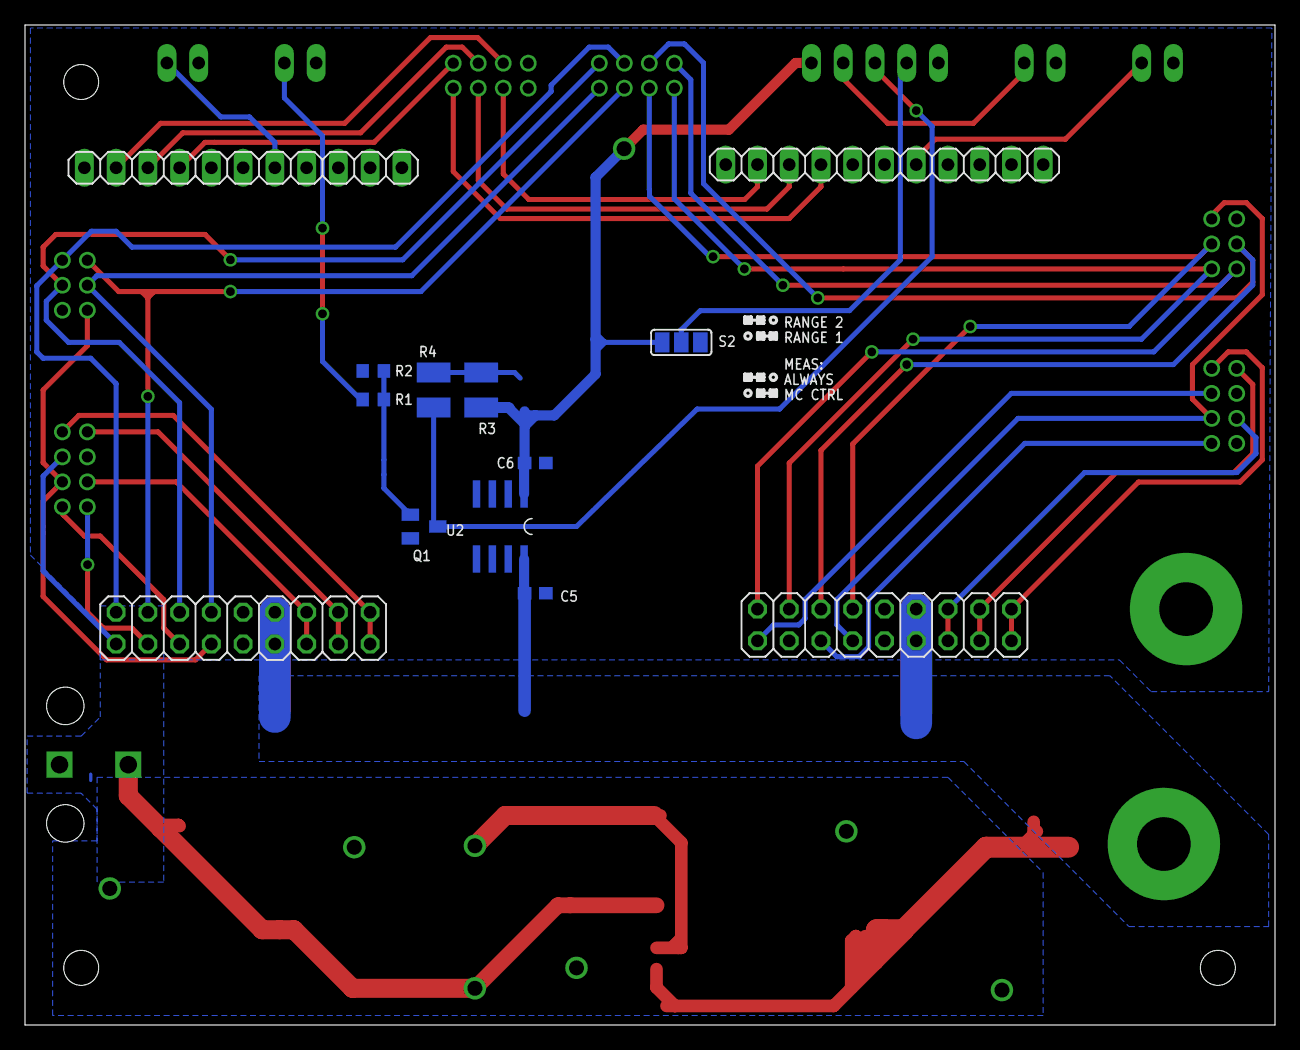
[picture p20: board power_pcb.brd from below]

Board: 8 copper layers, 100.0 x 80.0 mm, 37 parts (13 on the bottom side), 40 nets.

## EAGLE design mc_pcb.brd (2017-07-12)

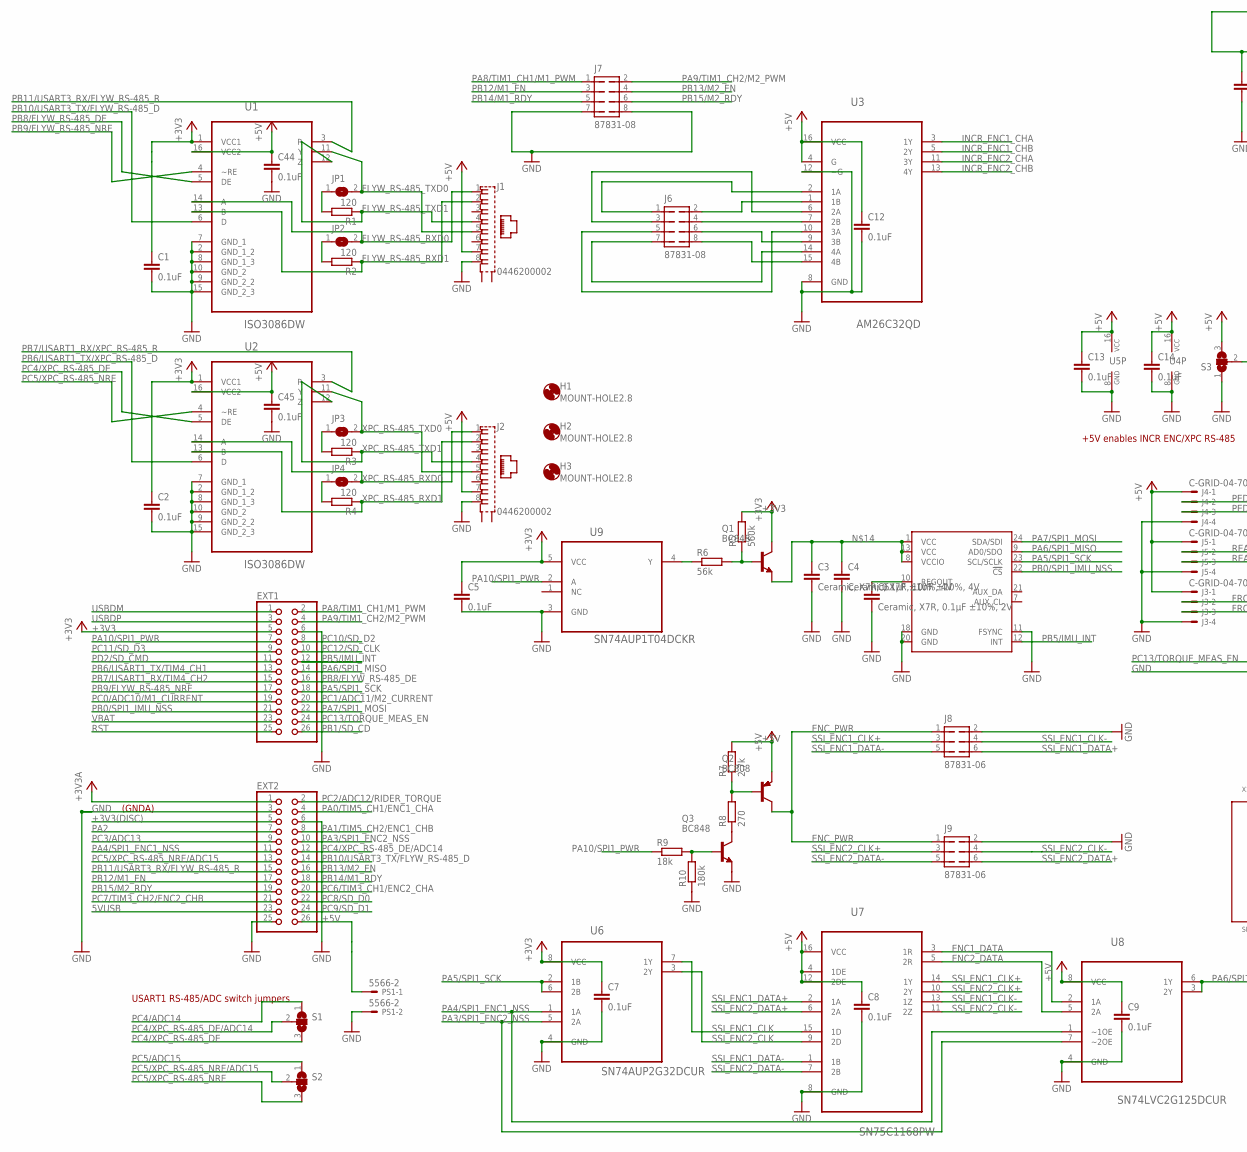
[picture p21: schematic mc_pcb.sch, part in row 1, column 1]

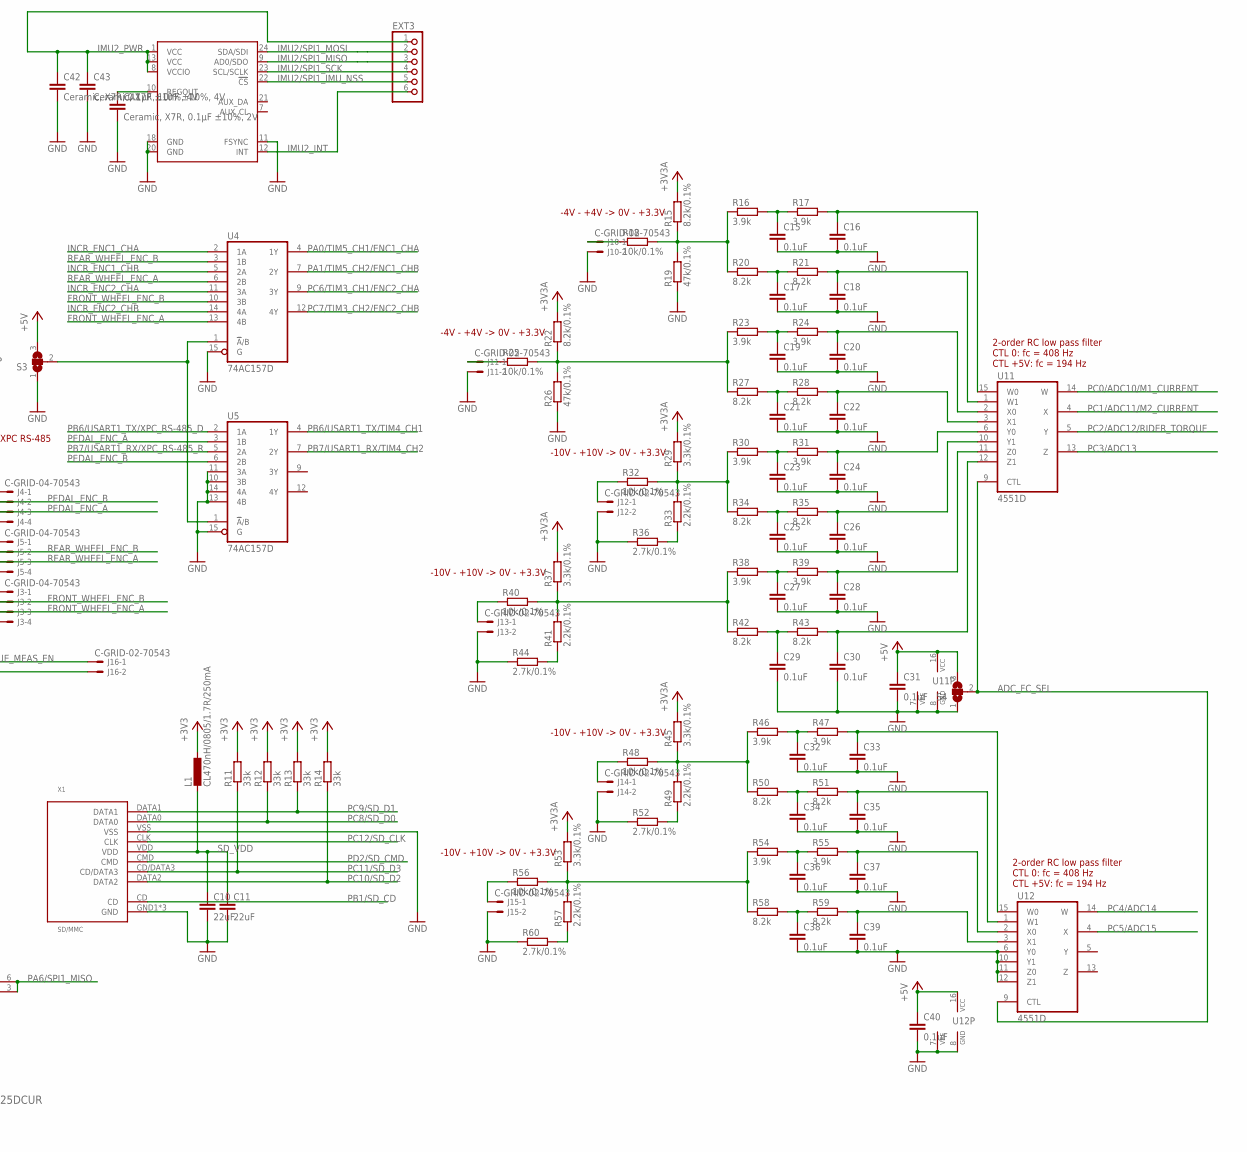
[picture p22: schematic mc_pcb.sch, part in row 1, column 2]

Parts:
C1, C2, C5, C7, C8, C9, C12, C13, C14, C15, C16, C17, C18, C19, C20, C21, C22, C23, C24, C25, C26, C27, C28, C29, C30, C31, C32, C33, C34, C35, C36, C37, C38, C39, C40, C44, C45: 0.1uF; C0603
C3, C42: Ceramic, X7R, 0.1μF ±10%, 4V; C0603
C4, C43: Ceramic, X7R, 10nF ±10%, 4V; C0603
C6, C41: Ceramic, X7R, 0.1μF ±10%, 2V; C0603
C10, C11: 22uF; C0603
EXT1, EXT2: PINHD-2X13; 2X13
EXT3: PINHD-1X6; 1X06
H1, H2, H3: MOUNT-HOLE2.8; 2,8
J1, J2: 0446200002
J3, J4, J5: C-GRID-04-70543; 70543-04
J6, J7: 87831-08
J8, J9: 87831-06
J10, J11, J12, J13, J14, J15, J16: C-GRID-02-70543; 70543-02
JP1, JP2, JP3, JP4: SJ
L1: CL470nH/0805/1.7R/250mA; L2012C
PS1: 5566-2
Q1, Q3: BC848; SOT23
Q2: BC808; SOT23-BEC
R1, R2, R3, R4: 120; R0603
R5: 560k; R0603
R6: 56k; R0603
R7: 2.7k; R1210
R8: 270; R1210
R9: 18k; R0603
R10: 180k; R0603
R11, R12, R13, R14: 33k; R0603
R15, R22: 8.2k/0.1%; R0603
R16, R17, R23, R24, R30, R31, R38, R39, R46, R47, R54, R55: 3.9k; R0603
R18, R25, R32, R40, R48, R56: 10k/0.1%; R0603
R19, R26: 47k/0.1%; R0603
R20, R21, R27, R28, R34, R35, R42, R43, R50, R51, R58, R59: 8.2k; R0603
R29, R37, R45, R53: 3.3k/0.1%; R0603
R33, R41, R49, R57: 2.2k/0.1%; R0603
R36, R44, R52, R60: 2.7k/0.1%; R0603
S1, S2, S3, S4: SJ2W; SJ_2
U1, U2: ISO3086DW; SOIC127P1030X265-16N
U3: AM26C32QD; SOIC127P600X175-16N
U4, U5: 74AC157D; SO16
U6: SN74AUP2G32DCUR; SOP50P310X90-8N
U7: SN75C1168PW; SOP65P640X120-16N
U8: SN74LVC2G125DCUR; SOP50P310X90-8N
U9: SN74AUP1T04DCKR; SOT65P210X110-5N
U10, U13: MPU-9250; QFN24-SMALL
U11, U12: 4551D; SO16
X1: 10100660; -68-6

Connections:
5VUSB: EXT2.23
+3V3: C1.1, C2.1, C5.1, C7.1, EXT1.5, L1.1, Q1.3 (C), R5.2, R11.2, R12.2, R13.2, R14.2, U1.1 (VCC1), U2.1 (VCC1), U6.8 (VCC), U9.5 (VCC)
+3V3(DISC): EXT2.5
+3V3A: EXT2.1, R15.2, R22.2, R29.2, R37.2, R45.2, R53.2
+5V: C8.1, C9.1, C12.1, C13.1, C14.1, C31.1, C40.1, C44.1, C45.1, EXT2.26, J1.7, J2.7, J3.1, J4.1, J5.1, PS1.1, Q2.E, R7.2, S3.3, S4.3, U1.16 (VCC2), U2.16 (VCC2), U3.4 (G), U3.16 (VCC), U4.16 (VCC), U5.16 (VCC), U7.4 (1DE), U7.12 (2DE), U7.16 (VCC), U8.8 (VCC), U11.16 (VCC), U12.16 (VCC)
ADC_FC_SEL: S4.2, U11.9 (CTL), U12.9 (CTL)
ENC1_CHA+: J6.2, U3.1 (1B)
ENC1_CHA-: J6.1, U3.2 (1A)
ENC1_CHB+: J6.4, U3.7 (2B)
ENC1_CHB-: J6.3, U3.6 (2A)
ENC1_DATA: U7.3 (1R), U8.2 (1A)
ENC2_CHA+: J6.6, U3.9 (3B)
ENC2_CHA-: J6.5, U3.10 (3A)
ENC2_CHB+: J6.8, U3.15 (4B)
ENC2_CHB-: J6.7, U3.14 (4A)
ENC2_DATA: U7.5 (2R), U8.5 (2A)
ENC_PWR: J8.1, J9.1, Q2.C
FLYW_RS-485_RXD0: J1.1, JP2.2, U1.14 (A)
FLYW_RS-485_RXD1: J1.2, R2.1, U1.13 (B)
FLYW_RS-485_TXD0: J1.5, JP1.2, U1.11 (Y)
FLYW_RS-485_TXD1: J1.4, R1.1, U1.12 (Z)
FRONT_WHEEL_ENC_A: J3.3, U4.13 (4B)
FRONT_WHEEL_ENC_B: J3.2, U4.10 (3B)
GND: C1.2, C2.2, C3.2, C4.2, C5.2, C6.2, C7.2, C8.2, C9.2, C10.2, C11.2, C12.2, C13.2, C14.2, C15.2, C16.2, C17.2, C18.2, C19.2, C20.2, C21.2, C22.2, C23.2, C24.2, C25.2, C26.2, C27.2, C28.2, C29.2, C30.2, C31.2, C32.2, C33.2, C34.2, C35.2, C36.2, C37.2, C38.2, C39.2, C40.2, C41.2, C42.2, C43.2, C44.2, C45.2, EXT1.6, EXT2.3, EXT2.6, EXT2.25, J1.8, J2.8, J3.4, J4.4, J5.4, J7.7, J7.8, J8.2, J9.2, J10.2, J11.2, J12.2, J13.2, J14.2, J15.2, J16.2, PS1.2, Q3.2 (E), R10.1, R19.1, R26.1, R36.1, R44.1, R52.1, R60.1, S3.1, S4.1, U1.2 (GND_1_2), U1.7 (GND_1), U1.8 (GND_1_3), U1.9 (GND_2_2), U1.10 (GND_2), U1.15 (GND_2_3), U2.2 (GND_1_2), U2.7 (GND_1), U2.8 (GND_1_3), U2.9 (GND_2_2), U2.10 (GND_2), U2.15 (GND_2_3), U3.8 (GND), U3.12 (~G), U4.8 (GND), U4.15 (G), U5.8 (GND), U5.10 (3B), U5.11 (3A), U5.13 (4B), U5.14 (4A), U5.15 (G), U6.4 (GND), U7.8 (GND), U8.4 (GND), U9.3 (GND), U10.11 (FSYNC), U10.18 (GND), U10.20 (GND), U11.7 (VEE), U11.8 (GND), U12.6 (Y0), U12.7 (VEE), U12.8 (GND), U12.10 (Y1), U12.11 (Z0), U12.12 (Z1), U13.11 (FSYNC), U13.18 (GND), U13.20 (GND), X1.GND1 (GND), X1.GND2 (GND), X1.GND3 (GND), X1.VSS
IMU2/SPI1_IMU_NSS: EXT3.5, U13.22 (!CS)
IMU2/SPI1_MISO: EXT3.3, U13.9 (AD0/SDO)
IMU2/SPI1_MOSI: EXT3.2, U13.24 (SDA/SDI)
IMU2/SPI1_SCK: EXT3.4, U13.23 (SCL/SCLK)
IMU2_INT: EXT3.6, U13.12 (INT)
IMU2_PWR: C42.1, C43.1, EXT3.1, U13.1 (VCC), U13.8 (VCCIO), U13.13 (VCC)
INCR_ENC1_CHA: U3.3 (1Y), U4.2 (1A)
INCR_ENC1_CHB: U3.5 (2Y), U4.5 (2A)
INCR_ENC2_CHA: U3.11 (3Y), U4.11 (3A)
INCR_ENC2_CHB: U3.13 (4Y), U4.14 (4A)
unnamed: C6.1, U10.10 (REGOUT)
unnamed: Q1.1 (B), R5.1, R6.2
unnamed: Q2.B, R7.1, R8.2
unnamed: Q3.3 (C), R8.1
unnamed: Q3.1 (B), R9.2, R10.2
unnamed: R33.1, R36.2
unnamed: R29.1, R30.1, R32.2, R33.2, R34.1
unnamed: C41.1, U13.10 (REGOUT)
unnamed: C3.1, C4.1, Q1.2 (E), U10.1 (VCC), U10.8 (VCCIO), U10.13 (VCC)
unnamed: R15.1, R16.1, R18.2, R19.2, R20.1
unnamed: R37.1, R38.1, R40.2, R41.2, R42.1
unnamed: JP1.1, R1.2
unnamed: JP3.1, R3.2
unnamed: C32.1, R46.2, R47.1
unnamed: C33.1, R47.2, U12.15 (W0)
unnamed: C34.1, R50.2, R51.1
unnamed: C35.1, R51.2, U12.1 (W1)
unnamed: C36.1, R54.2, R55.1
unnamed: C37.1, R55.2, U12.2 (X0)
unnamed: C38.1, R58.2, R59.1
unnamed: C39.1, R59.2, U12.3 (X1)
unnamed: R6.1, U9.4 (Y)
unnamed: J15.1, R56.1
unnamed: R22.1, R23.1, R25.2, R26.2, R27.1
unnamed: J14.1, R48.1
unnamed: S3.2, U4.1 (!A!/B), U5.1 (!A!/B)
unnamed: J12.1, R32.1
unnamed: JP2.1, R2.2
unnamed: JP4.1, R4.2
unnamed: J10.1, R18.1
unnamed: C23.1, R30.2, R31.1
unnamed: C24.1, R31.2, U11.6 (Y0)
unnamed: R41.1, R44.2
unnamed: R45.1, R46.1, R48.2, R49.2, R50.1
unnamed: R49.1, R52.2
unnamed: R53.1, R54.1, R56.2, R57.2, R58.1
unnamed: R57.1, R60.2
unnamed: J13.1, R40.1
unnamed: C25.1, R34.2, R35.1
unnamed: C26.1, R35.2, U11.10 (Y1)
unnamed: C27.1, R38.2, R39.1
unnamed: C28.1, R39.2, U11.11 (Z0)
unnamed: C29.1, R42.2, R43.1
unnamed: C30.1, R43.2, U11.12 (Z1)
unnamed: C15.1, R16.2, R17.1
unnamed: C16.1, R17.2, U11.15 (W0)
unnamed: C17.1, R20.2, R21.1
unnamed: C18.1, R21.2, U11.1 (W1)
unnamed: C19.1, R23.2, R24.1
unnamed: C20.1, R24.2, U11.2 (X0)
unnamed: C21.1, R27.2, R28.1
unnamed: C22.1, R28.2, U11.3 (X1)
PA0/TIM5_CH1/ENC1_CHA: EXT2.4, U4.4 (1Y)
PA1/TIM5_CH2/ENC1_CHB: EXT2.8, U4.7 (2Y)
PA2: EXT2.7
PA3/SPI1_ENC2_NSS: EXT2.10, U6.5 (2A), U8.7 (~2OE)
PA4/SPI1_ENC1_NSS: EXT2.11, U6.1 (1A), U8.1 (~1OE)
PA5/SPI1_SCK: EXT1.18, U6.2 (1B), U6.6 (2B), U10.23 (SCL/SCLK)
PA6/SPI1_MISO: EXT1.14, U8.3 (2Y), U8.6 (1Y), U10.9 (AD0/SDO)
PA7/SPI1_MOSI: EXT1.22, U10.24 (SDA/SDI)
PA8/TIM1_CH1/M1_PWM: EXT1.2, J7.1
PA9/TIM1_CH2/M2_PWM: EXT1.4, J7.2
PA10/SPI1_PWR: EXT1.7, R9.1, U9.2 (A)
PB0/SPI1_IMU_NSS: EXT1.21, U10.22 (!CS)
PB1/SD_CD: EXT1.26, X1.CD
PB5/IMU_INT: EXT1.12, U10.12 (INT)
PB6/USART1_TX/TIM4_CH1: EXT1.13, U5.4 (1Y)
PB6/USART1_TX/XPC_RS-485_D: U2.6 (D), U5.2 (1A)
PB7/USART1_RX/TIM4_CH2: EXT1.15, U5.7 (2Y)
PB7/USART1_RX/XPC_RS-485_R: U2.3 (R), U5.5 (2A)
PB8/FLYW_RS-485_DE: EXT1.16, U1.5 (DE)
PB9/FLYW_RS-485_NRE: EXT1.17, U1.4 (~RE)
PB10/USART3_TX/FLYW_RS-485_D: EXT2.14, U1.6 (D)
PB11/USART3_RX/FLYW_RS-485_R: EXT2.15, U1.3 (R)
PB12/M1_EN: EXT2.17, J7.3
PB13/M2_EN: EXT2.16, J7.4
PB14/M1_RDY: EXT2.18, J7.5
PB15/M2_RDY: EXT2.19, J7.6
PC0/ADC10/M1_CURRENT: EXT1.19, U11.14 (W)
PC1/ADC11/M2_CURRENT: EXT1.20, U11.4 (X)
PC2/ADC12/RIDER_TORQUE: EXT2.2, U11.5 (Y)
PC3/ADC13: EXT2.9, U11.13 (Z)
PC4/ADC14: S1.1, U12.14 (W)
PC4/XPC_RS-485_DE: S1.3, U2.5 (DE)
PC4/XPC_RS-485_DE/ADC14: EXT2.12, S1.2
PC5/ADC15: S2.1, U12.4 (X)
PC5/XPC_RS-485_NRE: S2.3, U2.4 (~RE)
PC5/XPC_RS-485_NRE/ADC15: EXT2.13, S2.2
PC6/TIM3_CH1/ENC2_CHA: EXT2.20, U4.9 (3Y)
PC7/TIM3_CH2/ENC2_CHB: EXT2.21, U4.12 (4Y)
PC8/SD_D0: EXT2.22, R12.1, X1.DATA0
PC9/SD_D1: EXT2.24, R13.1, X1.DATA1
PC10/SD_D2: EXT1.8, R14.1, X1.DATA2
PC11/SD_D3: EXT1.9, R11.1, X1.CD/DATA3
PC12/SD_CLK: EXT1.10, X1.CLK
PC13/TORQUE_MEAS_EN: EXT1.24, J16.1
PD2/SD_CMD: EXT1.11, X1.CMD
PEDAL_ENC_A: J4.3, U5.3 (1B)
PEDAL_ENC_B: J4.2, U5.6 (2B)
REAR_WHEEL_ENC_A: J5.3, U4.6 (2B)
REAR_WHEEL_ENC_B: J5.2, U4.3 (1B)
RST: EXT1.25
SD_VDD: C10.1, C11.1, L1.2, X1.VDD
SSI_ENC1_CLK: U6.7 (1Y), U7.15 (1D)
SSI_ENC1_CLK+: J8.3, U7.14 (1Y)
SSI_ENC1_CLK-: J8.4, U7.13 (1Z)
SSI_ENC1_DATA+: J8.6, U7.2 (1A)
SSI_ENC1_DATA-: J8.5, U7.1 (1B)
SSI_ENC2_CLK: U6.3 (2Y), U7.9 (2D)
SSI_ENC2_CLK+: J9.3, U7.10 (2Y)
SSI_ENC2_CLK-: J9.4, U7.11 (2Z)
SSI_ENC2_DATA+: J9.6, U7.6 (2A)
SSI_ENC2_DATA-: J9.5, U7.7 (2B)
USBDM: EXT1.1
USBDP: EXT1.3
VBAT: EXT1.23
X124: J11.1, R25.1
XPC_RS-485_RXD0: J2.1, JP4.2, U2.14 (A)
XPC_RS-485_RXD1: J2.2, R4.1, U2.13 (B)
XPC_RS-485_TXD0: J2.5, JP3.2, U2.11 (Y)
XPC_RS-485_TXD1: J2.4, R3.1, U2.12 (Z)

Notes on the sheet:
-4V - +4V -> 0V - +3.3V
2-order RC low pass filter CTL 0: fc = 408 Hz CTL +5V: fc = 194 Hz
-10V - +10V -> 0V - +3.3V
+5V enables INCR ENC/XPC RS-485
USART1 RS-485/ADC switch jumpers
(GNDA)

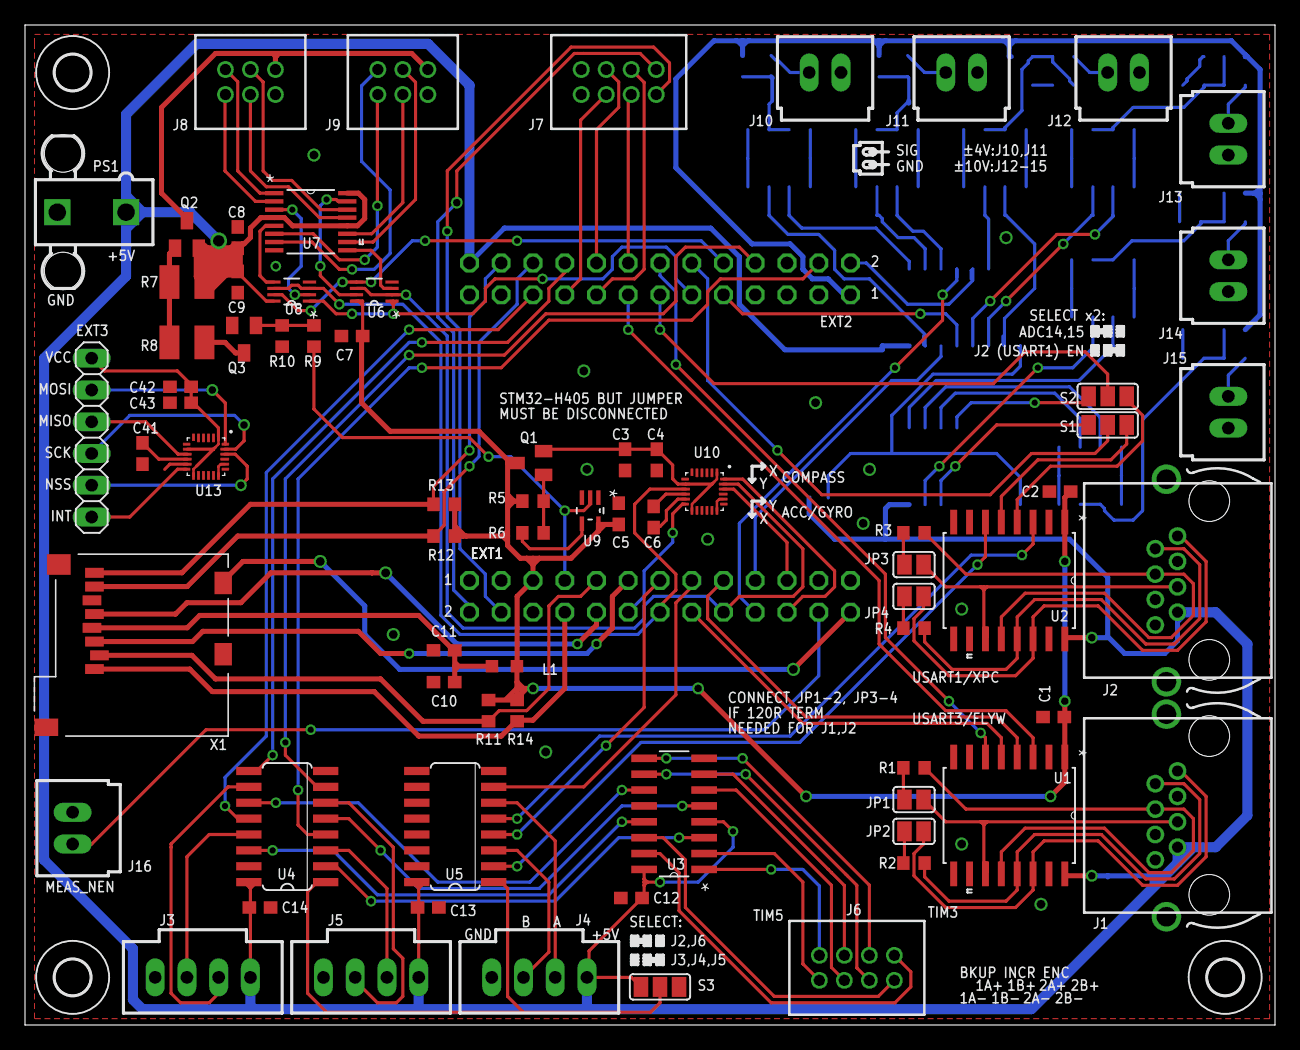
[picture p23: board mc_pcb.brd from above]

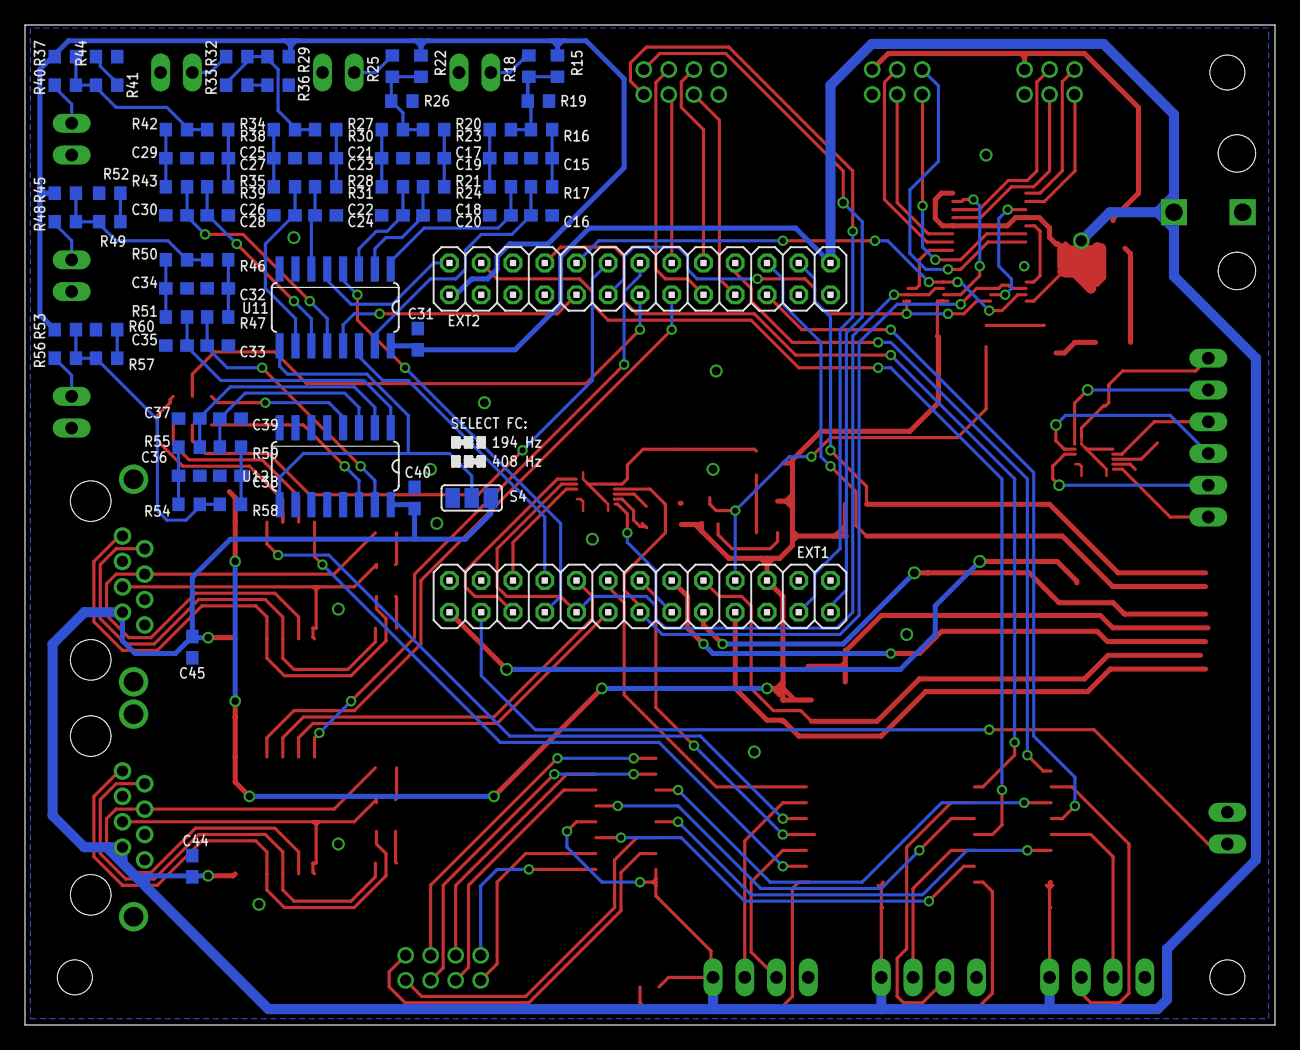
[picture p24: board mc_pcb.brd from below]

Board: 2 copper layers, 100.0 x 80.0 mm, 154 parts (79 on the bottom side), 148 nets.

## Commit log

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2015-12-07 Isolate voltage and ground supplies
    Create isolated analog ground, digital ground, and ground for DC-DC
    converter. Use analog +3.3V supply for analog low pass filters.
    [gyro_pcb.sch]
2015-12-07 Externally connect GND and GNDA
    Connect digital and analog grounds externally as stated in application
    note AN4488.
    [gyro_pcb.sch]
2015-12-09 Add RJ-45 connectors for RS-485
    Add RJ-45 connectors for flywheel and xpc target communication via
    RS-485. Connector pin-out follows specification for 2W-MODBUS RJ45.
    [gyro_pcb.sch]
2015-12-09 Add low-pass Butterworth filter for bike analog signals
    Add low-pass Butterworth filters for steer-by-wire bicycle pedal, front
    wheel, and rear wheel signals.
    [gyro_pcb.sch]
2015-12-09 Add analog input select jumpers
    Add jumpers to select between additional analog or quadrature encoder
    input.
    [gyro_pcb.sch]
2015-12-10 Add connector for torque sensor
    Add library for M12U 8-pole receiver for torque sensor connector. Add
    connector to schematic and measurement logic.
    [gyro_pcb.sch]
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2015-12-10 Fix SPI PWR switch connections
    [gyro_pcb.sch]
2015-12-10 Add connectors for analog inputs
    Add Molex 22-23-2041 solid header, vertical, with friction lock, 3 pin
    for analog inputs: pedal speed, front wheel speed, and rear wheel speed.
    [gyro_pcb.sch]
2015-12-10 Add connectors for analog tachometers
    Add connectors for DC motors used as tachometers for sensing pedal
    speed, front wheel speed, rear wheel speed. Voltage range from -10 V to
    +10V to reduced to 0 V to 3.3 V and pass through a 4th order low-pass
    Butterworth filter with cutoff frequency at 400 Hz.
    [gyro_pcb.sch]
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2015-12-10 Change connectors for analog input tachometers
    Replace with Molex SL headers.
    [gyro_pcb.sch]
2015-12-10 Add connectors for gear tooth encoders
    Gear tooth encoders use pinouts as specified in the GTS35/GTS45 gear
    tooth sensor datasheet. The PCB cannot be directly connected to the
    sensor as the connector used is a Molex SL header and an AMP 282088-1
    mating connector is required for the sensor cable.
    [gyro_pcb.sch]
2015-12-11 Add selection mux for bicycle encoder inputs
    Add jumper select between gyro backup encoders and XPC RS-485
    communication or bicycle rear, front, and pedal encoders.
    [gyro_pcb.sch]
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2015-12-11 Add regulated +18V supply to torque sensor
    Provide regulated +18V to torque sensor allowing for +24V or +36V
    batteries.
    [gyro_pcb.sch]
2015-12-11 Change values on resistors for torque measurement
    Increase resistor values for torque measurement switch.
    [gyro_pcb.sch]
2015-12-11 Fix incorrect NPN transistor in BJT switches
    [gyro_pcb.sch]
2015-12-11 Fix ERC errors
    [gyro_pcb.sch]
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2015-12-11 Remove encoder select mux
    The Olimex STM32-H4405 board has enough pins that the encoder mux is not
    necessary.
    [gyro_pcb.sch]
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2016-01-19 Create initial board layout
    Resistors and capacitors are grouped by subcircuit and still need to be
    placed correctly.
    [gyro_pcb.brd, gyro_pcb.sch]
2016-01-20 Add missing connectors for separate boards
    Add power and differential quadrature encoder connector. Place all
    components in board layout.
    [gyro_pcb.brd, gyro_pcb.sch]
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2016-01-20 Add ground plane, power traces
    Add ground plane, traces for +5V and +3V3A.
    [gyro_pcb.brd, gyro_pcb.sch]
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2016-01-22 Complete selectors for encoder/ADC input
    Complete labels for quad-mux ICs to select gimbal backup incremental
    encoders + XPC RS-485 or separate incremental encoder inputs. Add
    jumpers to receive ADC input over SPI ENC3,4.
    [gyro_pcb.brd, gyro_pcb.sch]
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2016-01-25 Fixup trace/pad connections and add vias to ground
    Move traces to touch pad corners. Add vias to ground for small ground
    traces. Increase clearance for connectors.
    [gyro_pcb.brd]
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2016-01-28 Mirror Olimex STM32-H405 on board layout
    Mirror Olimex on board so that pins are correctly defined for attaching
    board from top.
    [gyro_pcb.brd]
2016-01-28 Manually route board traces
    Define GND, GNDA planes. Define +5V, +3V3, +3V3A power traces. Begin
    route board components.
    [gyro_pcb.brd, gyro_pcb.sch]
2016-01-28 Swap pins used for ENC2 and IMU NSS
    Swap pins PA3, PB0 to PA3/SPI1_ENC2_NSS, PB0/SPI1_IMU_NSS to reduce
    trace length.
    [gyro_pcb.brd, gyro_pcb.sch]
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2016-01-28 Swap pins PA2, PA10
    Swap pins PA2, PA10 to PA2/SPI1_ENC1_STA, PA10/SPI1_PWR.
    [gyro_pcb.brd, gyro_pcb.sch]
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2016-01-28 Rename +3V3 pin on EXT2
    Rename pin to +3V3(DISC) and disconnect from +3V3 power supply to clear
    autorouting problems.
    [gyro_pcb.brd, gyro_pcb.sch]
2016-01-28 Fix silkscreen labels for STM32-H405 EXT
    Fix silkscreen labels for Olimex STM32-H405 EXT1 and EXT2. Label pins 1
    and 2 for each EXT.
    [gyro_pcb.brd]
2016-01-28 Place names of all components
    Place names of all components. This layer will not be included in the
    silkscreen layer due to the large amount of resistors and capacitors.
    [gyro_pcb.brd]
2016-01-29 Add silkscreen layer
    Add silkscreen layer with labels for connectors. Add descriptions for
    jumpers. Show coordinate axes for IMU.
    [gyro_pcb.brd]
2016-01-29 Move connector X3 and silkscreen labels
    Move connector X3 to allow pinout labels for connector X4.
    [gyro_pcb.brd]
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2016-02-03 Change torque measurement connector name
    Change torque measurement connector name to X15 to match microcontroller
    pcb.
    [power_pcb.brd, power_pcb.sch]
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2016-02-04 Add board and hole position dimensions
    Add board mount hole position dimensions. Change dimension units from
    mil to mm.
    [power_pcb.brd]
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2016-03-17 Merge GND and GNDA planes
    The analog signals are converted to 12-bit values and do not require a
    separate ground plane.
    [mc_pcb.brd, mc_pcb.sch, power_pcb.brd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]
2016-03-17 Copy +24V power trace and set clearance
    Copy +24V power track to bottom layer and set clearance to 12 mil
    (~0.3 mm).
    [power_pcb.brd, power_pcb.sch]
2016-03-17 Fix DRC clearance issues
    [power_pcb.brd]
2016-03-17 Open soldermask for +24V top power trace
    Draw tStop and tCream layers on +24 top power trace to increase current
    capacity.
    [power_pcb.brd]
2016-03-18 Change +24V connectors
    Change to holes and solder 6 AWG wires to board.
    [power_pcb.brd, power_pcb.sch]
2016-03-18 Add bypass capacitors
    Add missing bypass capacitors for buck circuit in power board and U3 in
    mc board.
    [mc_pcb.brd, mc_pcb.sch, power_pcb.brd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]
2016-03-18 Replace RS-485 half-duplex transceivers
    Use RS-485 full-duplex instead of half-duplex transceivers. Add STM32F4
    application note on ADC usage.
    [mc_pcb.brd, mc_pcb.sch]
2016-03-18 Change connector X15
    Change torque sensor measurement signal to active low and remove +3V3.
    [power_pcb.brd, power_pcb.sch]
2016-03-18 Replace Butterworth low pass filters
    Replace with 2-pole passive RC filters. Add solder switches to set
    cutoff frequency to 200 or 400 Hz.
    [mc_pcb.brd, mc_pcb.sch]
2016-03-19 Replace SPI encoders with SSI encoders
    Replace SPI encoders with RLS RMB20SC (SSI) 13-bit encoders in
    schematic. Add necessary ICs to use on SPI1 bus.
    [mc_pcb.brd, mc_pcb.sch]
2016-03-19 Add missing motor signal connector
    Add missing connector for PWM, EN, RDY signals for motors M1, M2. Use
    the same connector for SSI encoders and motor signals.
    [mc_pcb.brd, mc_pcb.sch]
2016-03-23 Finish component layout and routing
    Redo layout and routing after replacing RS-485 ICs, SSI encoders, analog
    filters.
    [mc_pcb.brd, mc_pcb.sch]
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2016-03-23 Fix values and packages for inductors and capacitors
    mc_pcb:
    Fix package size for L1 to 0805 (2012 metric) and value to 470 nH. Add
    additional value information for MPU9250 capacitors (C3, C4, C6).
    power_pcb:
    Change package of U2 to SO8. Fix values for C2, C3.
    [mc_pcb.brd, mc_pcb.sch, power_pcb.brd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]
2016-03-23 Fix buck converter inductor, capacitors
    Add SparkFun capacitor library containing PANASONIC_H13 package. In buck
    converter, fix package for C1, C2, L1 and rearrange traces.
    [power_pcb.brd, power_pcb.sch]
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2016-03-23 Fix reversed connector pinouts in power board
    Fix pinout for motor drive and connectors J6, J7.
    [power_pcb.brd, power_pcb.sch]
2016-03-23 Change connector for J5, J10, J11, J12
    Use Molex C-Grid 5 position connector for torque sensor J5. Reverse pins
    for analog connectors J10, J11, J12.
    [power_pcb.brd, power_pcb.sch]
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2016-03-25 Replace X1 with Amphenol micro SD socket
    [mc_pcb.brd, mc_pcb.sch]
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2016-03-29 Fix unconnected grounds
    [mc_pcb.brd]
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2016-03-29 Fix spacing of a few traces
    [mc_pcb.brd]
2016-03-29 Replace MPU-9250 component
    Add library for MPU-9250 component and replace in schematic.
    [mc_pcb.brd, mc_pcb.sch]
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2016-03-29 Fix drill distance to satisfy DRC
    [mc_pcb.brd, power_pcb.brd]
2016-03-30 Replace ISO35 with ISO30
    Replace ISO35 3.3V RS-485 transceiver with ISI3086 5V transceiver.
    [mc_pcb.brd, mc_pcb.sch]
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2016-04-01 Replace FPC connectors and route traces
    [mc_pcb.brd, mc_pcb.sch, power_pcb.brd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]
2016-06-10 Fix incorrect label for GPIOB_PIN11
    [mc_pcb.brd, mc_pcb.sch, power_pcb.brd]
2016-06-10 Add README with BOM and errata
    Add README with link to bill of materials and errata section.
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2016-09-30 Fix Kistler torque measurement line
    The Kistler torque sensor signal output line will only be valid if the
    measurement line pulled low after the sensor is powered on. The previous
    configuration with Q2 would not pull the measurement line to ground. As
    Q2 has been removed, the line name has changed from 'TORQUE_MEAS_NEN' to
    'TORQUE_MEAS_EN'.
    [mc_pcb.brd, mc_pcb.sch, power_pcb.brd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]
2016-10-13 Update README.md
    Silkscreen wrong for motor connectors
2016-10-21 Update README.md
    Hall sensor for motor 2 has missing trace
2016-10-21 Note missing pullup resistor for SDIO CMD
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

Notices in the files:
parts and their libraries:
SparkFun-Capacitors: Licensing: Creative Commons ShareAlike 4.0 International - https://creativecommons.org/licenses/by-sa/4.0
